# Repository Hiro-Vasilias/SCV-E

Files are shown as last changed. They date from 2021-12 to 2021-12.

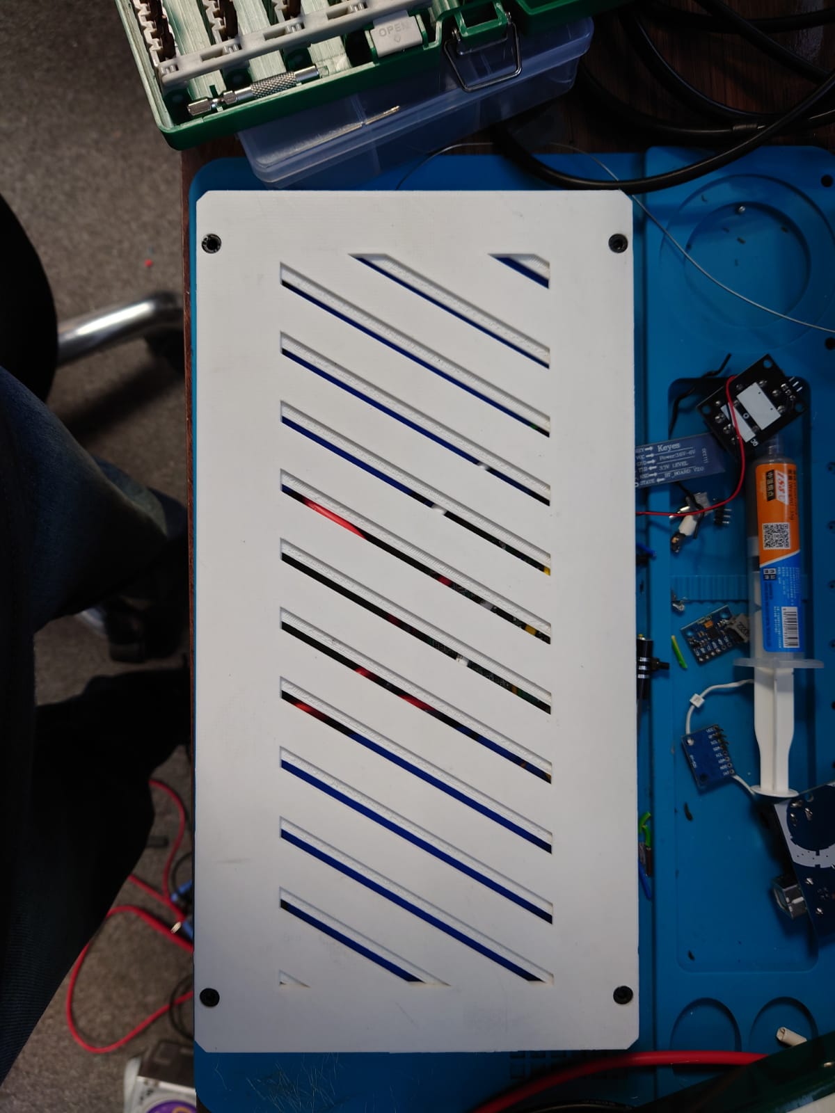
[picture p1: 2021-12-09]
Images/WhatsApp Image 2021-12-09 at 1.58.52 AM.jpeg

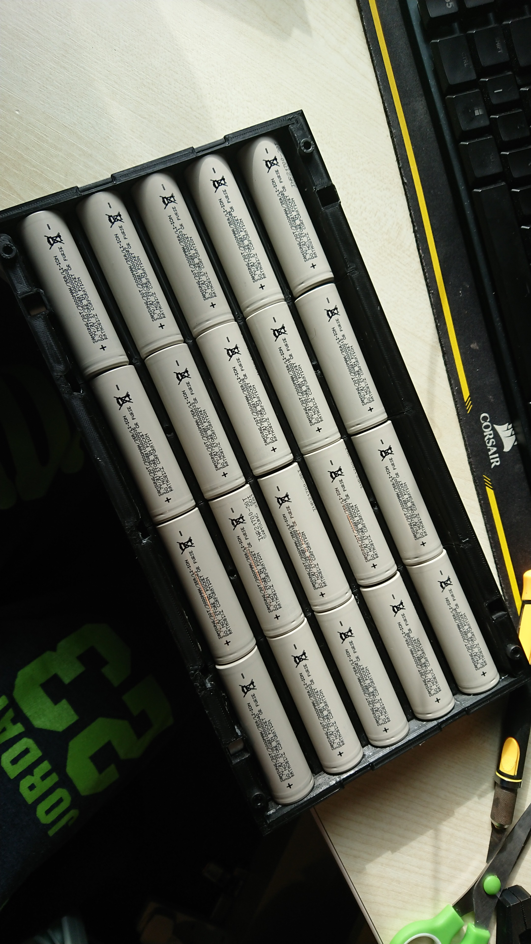
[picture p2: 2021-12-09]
Images/IMG-20210303-WA0010.jpg

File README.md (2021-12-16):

# SCV-E [Smart Construction Vehicle - Electric]
Modular vehicle for construction and transport

<<<<<<<<<<<<Contents>>>>>>>>>>>
  
  Documentation PROJ324.docx contains the documentation of the project submitted to the DLE.
  
  Proj324.xlsx contains the Budget costs and summary along with the Gantt chart.
  
  Buggy V2 V17.f3z contains the Design files Fusion 360
  
  Images Proj324 folder contains the images supporting this project.
  
  The rest shown are the programming code as shown in the document appendix

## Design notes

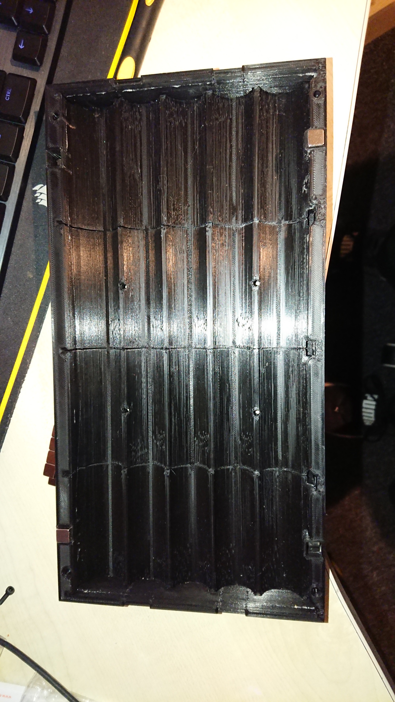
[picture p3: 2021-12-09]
Images/IMG-20210302-WA0009.jpg

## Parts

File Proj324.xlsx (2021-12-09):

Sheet: ProjectSchedule
Create a Project Schedule in this worksheet. Enter title of this project in cell B1. Information about how to use this worksheet, including instructions for screen readers and the author of this workbook is in the About worksheet. Continue navigating down column A to hear further instructions. | PROJ324 - SCV-E
Enter Company Name in cell B2. | Student 10588101
Enter the name of the Project Lead in cell B3. Enter the Project Start date in cell E3. Pooject Start: label is in cell C3. | Zil-E-Hasnain Shah | Project Start: |  | 2020-11-20
The Display Week in cell E4 represents the starting week to display in the project schedule in cell I4. The project start date is considered Week 1. To change the display week, simply enter a new week number in cell E4. The starting date for each week, starting with the display week from cell E4, starts in cell I4 and is auto calculated. There are 8 weeks represented in this view from cell I4 through cell BF4. You should not modify these cells. Display Week: label is in cell C4. |  | Display Week: |  | 1 |  | 2020-11-16 |  |  |  |  |  |  | 2020-11-23 |  |  |  |  |  |  | 2020-11-30 |  |  |  |  |  |  | 2020-12-07 |  |  |  |  |  |  | 2020-12-14 |  |  |  |  |  |  | 2020-12-21 |  |  |  |  |  |  | 2020-12-28 |  |  |  |  |  |  | 2021-01-04
Cells I5 through BL5 contain the day number for the week represented in the cell block above each date cell and are auto calculated. You should not modify these cells. Today's date is outlined in Red (hex #AD3815) from today's date in row 5 through the entire date column to the end of the project schedule. |  |  |  |  |  | 2020-11-16 | 2020-11-17 | 2020-11-18 | 2020-11-19 | 2020-11-20 | 2020-11-21 | 2020-11-22 | 2020-11-23 | 2020-11-24 | 2020-11-25 | 2020-11-26 | 2020-11-27 | 2020-11-28 | 2020-11-29 | 2020-11-30 | 2020-12-01 | 2020-12-02 | 2020-12-03 | 2020-12-04 | 2020-12-05 | 2020-12-06 | 2020-12-07 | 2020-12-08 | 2020-12-09 | 2020-12-10 | 2020-12-11 | 2020-12-12 | 2020-12-13 | 2020-12-14 | 2020-12-15 | 2020-12-16 | 2020-12-17 | 2020-12-18 | 2020-12-19 | 2020-12-20 | 2020-12-21 | 2020-12-22 | 2020-12-23 | 2020-12-24 | 2020-12-25 | 2020-12-26 | 2020-12-27 | 2020-12-28 | 2020-12-29 | 2020-12-30 | 2020-12-31 | 2021-01-01 | 2021-01-02 | 2021-01-03 | 2021-01-04 | 2021-01-05 | 2021-01-06
This row contains headers for the project schedule that follows below them. Navigate from B6 through BL 6 to hear the content. The first letter of each day of the week for the date above that heading, starts in cell I6 and continues through cell BL6. All project timeline charting is auto generated based on the start and end dates entered, using conditional formats. Do not modify content in cells within columns after column I starting with cell I7. | TASK | ASSIGNED TO | PROGRESS | START | END | M | T | W | T | F | S | S | M | T | W | T | F | S | S | M | T | W | T | F | S | S | M | T | W | T | F | S | S | M | T | W | T | F | S | S | M | T | W | T | F | S | S | M | T | W | T | F | S | S | M | T | W
Cell B8 contains the Phase 1 sample title. Enter a new Title in cell B8. Enter a name to assign the phase to, if it applies for your project, in cell C8. Enter Progress for the entire phase, if it applies for your project, in cell D8. Enter the start and end dates for the entire phase, if it applies for your project, in cells E8 and F8. The Gantt chart will automatically fill in the appropriate dates and shade according to the progress entered. To delete the phase and work only from tasks, simply delete this row. | Research Phase
Cell B9 contains the sample task "Task 1." Enter a new task name in cell B9. Enter a person to assign the task to in cell C9. Enter progres of the task in cell D9. A progress bar appears in the cell and is shaded according to the number in the cell. For example, 50 percent progress would shade half of the cell. Enter task start date in cell E9. Enter task end date in cell F9. A status bar shaded for the dates entered appears in blocks starting from cell I9 through BL9. | Construction vehicle |  | 100% | 2020-11-20 | 2020-11-20
Rows 10 through 13 repeat the pattern from row 9. Repeat the instructions from cell A9 for all task rows in this worksheet. Overwrite any sample data. A sample of another phase starts in cell A14. Continue entering tasks in cells A10 through A13 or go to cell A14 to learn more. | Batteries |  | 100% | 2020-12-01 | 2021-04-05
 | Crane |  | 100% | 2021-08-08 | 2021-11-20
 | Controller market |  | 100% | 2021-02-16 | 2021-03-21
 | Componets research |  | 100% | 2020-11-20 | 2021-01-01
 | Platform software |  | 100% | 2020-12-02 | 2020-12-04
The cell at right contains the Phase 2 sample title. You can create a new phase at any time within column B. This project schedule does not require phases. To remove the phase, simply delete the row. To create a new phase block in this row, enter a new Title in cell at right. To continue adding tasks to the phase above, enter a new row above this one and fill in the task data as in cell A9's instruction. Update the Phase details in cell at right based on cell A8's instruction. Continue navigating down column A cells to learn more. If you haven't added any new rows in this worksheet, you will find 2 additional sample phase blocks have been created for you in cells B20 and B26. Otherwise, navigate through column A cells to find the additional blocks. Repeat the instructions from cells A8 and A9 whenever you need to. | Design Phase
 | Initial CAD model of SCV |  | 100% | 2020-12-03 | 2021-01-12
 | Re-itereation of SCV |  | 100% | 2021-04-03 | 2021-07-25
 | PCB Circuit for SCV |  | 100% | 2021-10-01 | 2021-11-01
 | PCB Circuit for Controller |  | 100% | 2020-11-20 | 2021-02-16
 | CAD model of controller | 80% | 100% | 2021-02-20 | 2021-06-06
 | CAD model of base station |  | 100% | 2020-12-12 | 2021-03-25
Sample phase title block | Manufacturing Phase
 | 3D printing |  | 100% | 2020-12-05 | 2021-12-07
 | Assembling Controller |  | 100% | 2021-05-05 | 2021-08-08
 | Assembling base station | 80% | 100% | 2021-05-10 | 2021-05-15
 | Assembling SCV |  | 100% | 2021-05-16 | 2021-12-06
 | Programming Base station |  | 100% | 2021-09-01 | 2021-09-05
 | Programming SCV |  | 100% | 2021-07-06 | 2021-12-06
 | Assembling Makeshift Controller |  | 100% | 2021-11-26 | 2021-11-30
 | Programming Controller |  | 100% | 2021-12-01 | 2021-12-06
Sample phase title block | Testing
 | Controller |  | 100% | 2021-12-02 | 2021-12-06
 | SCV |  | 100% | 2021-12-02 | 2021-12-06
 | Deliverable
 | Main components delivered |  | 100% | 2021-01-01 | 2021-04-06
 | Second batch components delivered |  | 100% | 2021-05-15 | 2021-06-01
 | Third batch components delivered |  | 100% | 2021-10-02 | 2021-11-02
 | Disruption during project
 | Covid Self isolation #1 |  | 100% | 2020-12-26 | 2021-01-14
 | Covid Self isolation #2 |  | 100% | 2021-08-14 | 2021-08-30
 | Family Death Covid |  | 100% | 2021-05-06 | 2021-05-06
 | Family Death Covid |  | 100% | 2021-08-07 | 2021-08-07
This is an empty row
This row marks the end of the Project Schedule. DO NOT enter anything in this row. Insert new rows ABOVE this one to continue building out your Project Schedule. | Insert new rows ABOVE this one

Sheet: BUDGET SUMMARY
 |  | Itemized Expenses
PROJ324 | PROJECT BUDGET
PROJECT INFORMATION
Project Name | SCV-E
Project Description | Dump Truck Type Buggy with Crane lifter and Live Video Feedback, Charging base and Custom Controller included
Contractor | -
Student ID | 10588101
Student Name | Hasnain Shah
OneNote Link | PROJECT SHOWCASE (https://liveplymouthac.sharepoint.com/sites/Projects-PROJ324PROJ325/_layouts/15/Doc.aspx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)
SuperVisor | Shakil Awan Ahmed
FullFilled Date | 9th december 2021
FINANCIAL STATUS
Planned Amount | £500.00
Sponsored Amount | £250.00
Additional Amount put in | £1500.00
Loaned Amount | £500.00
Total Allotted Funds | £2750.00
Funds Used To Date | £2740.91
Project Cost | £667.85
Funds Remaining | £9.09

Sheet: ITEMIZED EXPENSES
 |  |  |  |  |  |  |  |  | Budget Summary
LIST | OF EXPENSES
PROJECT FUNDS ALLOTTED |  | FUNDS USED TO DATE |  |  | PROJECT COST |  |  | FUNDS REMAINING
£2750.00 |  | £2740.91 |  |  | £667.85 |  |  | £9.09
Item | Supplier | Category | Type | QTY | Purchase Cost | Price Per QTY | Used QTY | Used Cost
TS5828s 200MW 5.8G 40ch FPV Camera | AliExpress | Materials | Buggy | 1 | £17.78 | £17.78 | 1 | £17.78
50 Pairs Metal Battery Spring plate | AliExpress | Materials | Buggy | 50 | £3.33 | £0.07 | 0 | £0.00
GT-24 Wireless module 2.4G NRF24L01 | AliExpress | Materials | Buggy | 1 | £2.24 | £2.24 |  | £0.00
Mechanic UV Solder Mask INK PCB | AliExpress | Equipment | All | 1 | £3.63 | £3.63 | 0.5 | £1.81
N35 Neodymium magnets | AliExpress | Materials | Base Station | 50 | £4.25 | £0.09 | 4 | £0.34
N50 Neodymium magnets | AliExpress | Materials | Buggy | 20 | 8 | £0.40 | 8 | £3.20
50N Solenoid Electromagnet 5V + IP65 | AliExpress | Materials | Buggy | 1 | £2.68 | £2.68 | 1 | £2.68
25N Solenoid Electromagnet 5V + IP65 | AliExpress | Materials | None | 1 | £1.97 | £1.97 | 0 | £0.00
Crocodile Clips | AliExpress | Equipment | All | 10 | £1.27 | £0.13 | 0 | £0.00
Mechanic Paste Flux 10CC SMD PCB | AliExpress | Equipment | All | 2 | £3.75 | £1.88 | 0.5 | £0.94
Alligator test clip to Jumper cable 30cm | AliExpress | Equipment | All | 5 | £2.16 | £0.43 | 5 | £2.16
Toggle Switch 125V 6A ON-ON 2POS+3PIN | AliExpress | Materials | Controller | 5 | £2.55 | £0.51 |  | £0.00
Potentiometer 10K ohm | AliExpress | Materials | Controller | 5 | £1.91 | £0.38 |  | £0.00
100x100 mm Thermal Pad heatsink | AliExpress | Materials | Buggy | 2 | £6.71 | £3.35 | 2 | £6.71
4S 40A BMS LIPO with balancer | AliExpress | Materials | Buggy | 1 | £3.33 | £3.33 | 1 | £3.33
SMD LED 5730 kit | AliExpress | Materials | None | 100 | £2.10 | £0.02 |  | £0.00
BGA Reballing 1 Bottle 0.76 mm | AliExpress | Materials | None | 1 | £1.37 | £1.37 | 0 | £0.00
GT-24 Wireless module 2.4G NRF24L01 | AliExpress | Materials | Controller | 1 | £2.24 | £2.24 | 1 | £2.24
Type C PD3.0 Trigger Spoof | AliExpress | Materials | None | 1 | £5.74 | £5.74 | 1 | £5.74
15W Qi Wireless charger | AliExpress | Materials | Base Station | 1 | £8.28 | £8.28 | 1 | £8.28
Battery Insulator gasket 1000x120 mm | AliExpress | Materials | B+C | 1 | £1.65 | £1.65 |  | £0.00
4PCS 110x48 mm 1/10 Wheel set | AliExpress | Materials | Buggy | 4 | £14.90 | £3.73 | 4 | £14.90
Push button Vertical Set 4 pin | AliExpress | Materials | Controller | 100 | £2.56 | £0.03 | 10 | £0.26
4x360 Servo 35KG | AliExpress | Materials | Buggy | 4 | £30.59 | £7.65 | 5 | £38.24
ESD Heat soldering Mat | AliExpress | Materials | All | 1 | £8.29 | £8.29 |  | £0.00
DC Motor 5-200 rpm Hall Encoder | AliExpress | Materials | Buggy | 4 | £23.21 | £5.80 | 4 | £23.21
Micro Switches assorted 10 type ea | AliExpress | Materials | Controller | 100 | £3.55 | £0.04 |  | £0.00
JST-XH JST + Dupont connector Kit + crimping tool | AliExpress | Materials | All | 1080 | £15.94 | £0.01 | 5 | £0.07
5000 mAh Li-po Batteries 3.7V | AliExpress | Materials | Controller | 4 | £11.73 | £2.93 | 0 | £0.00
10000 mAh Li-po Batteries 3.7V | AliExpress | Materials | None | 2 | £9.60 | £4.80 | 0 | £0.00
Panasonic 21700 4800mAh +PCB 40A | AliExpress | Loss (Scammed) | Buggy | 40 | £80.31 | £2.01 | 0 | £0.00
Carbon Fiber Hydro dip | AliExpress | Materials | Controller | 1 | £5.92 | £5.92 |  | £0.00
Joystick 3D analog PS2 | AliExpress | Materials | Controller | 4 | £2.84 | £0.71 | 2 | £1.42
SMD LED 5050 RGB | AliExpress | Materials | None | 100 | £1.66 | £0.02 |  | £0.00
Type C PD3.0 20V | AliExpress | Materials | Base Station | 1 | £1.45 | £1.45 | 1 | £1.45
Type C PD3.0 9V | AliExpress | Materials | Controller | 1 | £1.45 | £1.45 | 1 | £1.45
GY-521 MPU 6050 accelerometer | AliExpress | Materials | Controller | 1 | £6.75 | £6.75 | 1 | £6.75
E-DA TPU 1KG 1.75 mm Filament (Price per gram) | Amazon | Materials | All | 1000 | £20.98 | £0.02 |  | £0.00
Gorilla Wood Glue 1L | Amazon | Equipment | Base Station | 1 | £9.00 | £9.00 |  | £0.00
Gorilla Super Glue 12g | Amazon | Equipment | All | 1 | £4.80 | £4.80 |  | £0.00
Gorilla Glue Contact Adhesive 75g | Amazon | Equipment | B+BS | 1 | £6.68 | £6.68 |  | £0.00
Dremel Moto scroll saw MS20 | Amazon | Equipment | All | 1 | £100.26 | £100.26 |  | £0.00
Banana Plug connector | Amazon | Materials | Buggy | 20 | £7.99 | £0.40 | 10 | £4.00
Anycubic 3D printer PLA 1KG | Amazon | Materials | All | 1000 | £21.99 | £0.02 |  | £0.00
LACO125AMZ-LA-CO Flux paste 125g | Amazon | Materials | All | 1 | £5.75 | £5.75 |  | £0.00
Hurricane 3 pc Pliers Set | Amazon | Equipment | All | 3 | £18.99 | £6.33 |  | £0.00
Copper Sheet 0.4x300x210 mm | Amazon | Materials | Buggy | 2 | £22.00 | £11.00 | 1.5 | £16.50
DC PSU LAB power bench 30V-10A max | Amazon | Equipment | All | 1 | £72.99 | £72.99 |  | £0.00
Resistor kit 1% 1/4 | Amazon | Materials | All | 1050 | £12.99 | £0.01 | 20 | £0.25
LED 5 mm | Amazon | Materials | B+C | 500 | £6.99 | £0.01 |  | £0.00
PLA Filament 1 KG Generic Gray | Volt3D | Materials | All | 1000 | £10.00 | £0.01 | 1 | £0.01
PLA Filament 1 KG Evryone Black | Amazon | Materials | All | 1000 | £17.99 | £0.02 | 1 | £0.02
PLA Filament 1KG Evryone Glitter Black | Amazon | Materials | All | 1000 | £17.99 | £0.02 |  | £0.00
Wifi Router Attenna IPEX4 | Amazon | Materials | Controller | 2 | £8.49 | £4.25 | 2 | £8.49
Arduino Nano 33 BLE Sense [ABX00031] | Amazon | Materials | Controller | 1 | £35.40 | £35.40 | 0 | £0.00
5.8G mini 72CH 200mW Eachine VTX03 | Banggood | Materials | Buggy | 1 | £8.96 | £8.96 |  | £0.00
Foxeer Razer 5MP HD Camera | Banggood | Materials | Buggy | 1 | £16.78 | £16.78 | 1 | £16.78
RX5805 5.8Ghz 48ch 480x320 5'' monitor | Banggood | Materials | Controller | 1 | £20.45 | £20.45 | 0 | £0.00
Simax3D Magnetic 3D printer Bed | Banggood | Replacement | All | 1 | £7.70 | £7.70 |  | £0.00
Hotend 24V 40W (creality) | Banggood | Replacement | All | 1 | £8.30 | £8.30 |  | £0.00
21700 Insulators | Fogstar Wholesale UK | Materials | Buggy | 100 | £4.00 | £0.04 | 1 | £0.04
21700 PVC Wraps - Black | Fogstar Wholesale UK | Materials | Buggy | 40 | £2.10 | £0.05 | 1 | £0.05
Samsung 21700 30T - 3.7V 30A | Fogstar Wholesale UK | Materials | Buggy | 40 | £115.60 | £2.89 | 22 | £63.58
Efest V8 - 21700 cell charger | Fogstar Wholesale UK | Equipment | All | 1 | £24.45 | £24.45 |  | £0.00
MDF 2440x1220 | B&Q UK | Materials | Base Station | 3 | £45.00 | £15.00 | 2.7 | £40.50
Controller Custom PCB [Y1-3442490B] | JCLB | Materials | Controller | 5 | £15.36 | £3.07 | 2 | £6.14
Micro JST PH2.0 2-pin plugs 10cm | Amazon | Materials | Controller | 20 | £5.99 | £0.30 |  | £0.00
Choetecth USB C PD100W | Amazon | Equipment | Base Station | 1 | £49.99 | £49.99 | 1 | £49.99
Inductor 0.5W 1/2W | Amazon | Materials | All | 200 | £12.99 | £0.06 | 2 | £0.13
3 pin SPDT mini slide switch | Amazon | Materials | All | 55 | £7.49 | £0.14 | 2 | £0.27
Capacitor assortment kit | Amazon | Materials | All | 600 | £15.99 | £0.03 | 2 | £0.05
22AWG PVC 9M spool Blue (Price per cm) | Amazon | Materials | All | 900 | £2.33 | £0.002592222222 | 30 | £0.08
22AWG PVC 9M spool Black (Price per cm) | Amazon | Materials | All | 900 | £2.33 | £0.002588888889 | 40 | £0.10
22AWG PVC 9M spool Green (Price per cm) | Amazon | Materials | All | 900 | £2.33 | £0.002588888889 | 50 | £0.13
22AWG PVC 9M spool White (Price per cm) | Amazon | Materials | All | 900 | £2.33 | £0.002588888889 | 10 | £0.03
22AWG PVC 9M spool Yellow(Price per cm) | Amazon | Materials | All | 900 | £2.33 | £0.002588888889 | 5 | £0.01
22AWG PVC 9M spool Red (Price per cm) | Amazon | Materials | All | 900 | £2.33 | £0.002588888889 | 40 | £0.10
Arduino Mega 2560 Rev3 [A000067] | Amazon | Materials | Buggy | 1 | £35.70 | £35.70 | 0 | £0.00
YIXISI High Temperature Kapton Tape 3mm | Amazon | Materials | All | 330 | £1.76 | £0.01 |  | £0.00
YIXISI High Temperature Kapton Tape 6mm | Amazon | Materials | All | 330 | £1.76 | £0.01 |  | £0.00
YIXISI High Temperature Kapton Tape 8mm | Amazon | Materials | All | 330 | £1.76 | £0.01 |  | £0.00
YIXISI High Temperature Kapton Tape 10mm | Amazon | Materials | All | 330 | £1.76 | £0.01 |  | £0.00
YIXISI High Temperature Kapton Tape 12mm | Amazon | Materials | All | 330 | £1.76 | £0.01 |  | £0.00
YIXISI High Temperature Kapton Tape 20mm | Amazon | Materials | All | 330 | £1.76 | £0.01 | 30 | £0.16
Arduino Mega R3 Elegoo | Amazon | Materials | Buggy | 1 | £11.89 | £11.89 | 1 | £11.89
PLA Filament ppx Black | Amazon | Materials | Controller | 1 | 18.38 | £18.38 | 1 | £18.38
First Aid Kit pack of 100 | Amazon | Safety | Human | 100 | 9.49 | £0.09 | 12 | £1.14
The One Paint Satin White + Dark Grey# | Amazon | Materials | Base Station | 1 | 37.98 | £37.98 | 0 | £0.00
Electric paint sprayer | Amazon | Equipment | All | 1 | 32.53 | £32.53 |  | £0.00
MDF Primer White | Amazon | Materials | Base Station | 1 | 9.9 | £9.90 |  | £0.00
Chisel Set tools | Amazon | Equipment | All | 1 | 27.99 | £27.99 | 0.2 | £5.60
Belt Sander Rent | Machinemarkt | Equipment | Base Station | 1 | 15.99 | £15.99 | 0 | £0.00
Geetech PETG Filament | Amazon | Materials | All | 1 | 23.99 | £23.99 | 1 | £23.99
Elegoo Mars Pro SLA printer | Amazon | Equipment | All | 1 | 130 | £130.00 |  | £0.00
Elegoo LCD UV 405nm ABS | Amazon | Materials | All | 1 | 38 | £38.00 |  | £0.00
Rubber Mallet fiberglas | Amazon | Equipment | All | 1 | 14.95 | £14.95 |  | £0.00
Primacreator Value UV FLEX resin | Amazon | Materials | All | 1 | 34.38 | £34.38 |  | £0.00
10 pin rainbow flat ribbon cable | Amazon | Materials | All | 1 | 7.19 | £7.19 |  | £0.00
Tronxy X5SA pro printer | Machinemarkt | Equipment | All | 1 | 339.98 | £339.98 | 0.1 | £34.00
Tecbears PLA Filament | Amazon | Materials | All | 5 | 64.95 | £12.99 | 4 | £51.96
Tecbears Petg Filament | Amazon | Materials | All | 1 | 11.99 | £11.99 |  | £0.00
Ball Bearing 8mm x22 mm x7 mm | Amazon | Materials | All | 8 | 6.49 | £0.81 | 3 | £2.43
HSS step drill bits | Amazon | Equipment | All | 3 | 12.34 | £4.11 |  | £0.00
GT2 Pulley 8mm bore 6mm width | Amazon | Materials | All | 10 | 7.99 | £0.80 | 4 | £3.20
Deburing tool | Amazon | Equipment | All | 1 | 12.73 | £12.73 |  | £0.00
3D printer Glass platform holder | Amazon | Equipment | All | 100 | 7.99 | £0.08 | 4 | £0.32
Cable ties 100 | Amazon | Materials | All | 100 | 2.99 | £0.03 | 25 | £0.75
Tool star lock washers stainless steel | Amazon | Materials | All | 300 | 10.44 | £0.03 | 3 | £0.10
Dremel Workstation 220 | Amazon | Equipment | All | 1 | 29.24 | £29.24 |  | £0.00
PCA9685 16 channel | Amazon | Materials | Buggy | 2 | 7.59 | £3.79 | 1 | £3.79
360 pcs dupont wire | Amazon | Materials | All | 360 | 9.99 | £0.03 | 100 | £2.77
L298N stepper motor driver | Amazon | Materials | Buggy | 5 | 9.99 | £2.00 | 3 | £5.99
Fuse wire | Amazon | Materials | Buggy | 3 | 2.9 | £0.97 | 1 | £0.97
Fuse holder | Amazon | Materials | Buggy | 1 | 2.99 | £2.99 | 1 | £2.99
Reed Magnetic switch | Amazon | Materials | Buggy | 10 | 7.99 | £0.80 |  | £0.00
150 mm linear actuator | Amazon | Materials | Buggy | 1 | 29.9 | £29.90 | 1 | £29.90
Dremel MS53 Saw blades | Amazon | Equipment | All | 5 | 6 | £1.20 | 3 | £3.60
Arduino BLE-NANO replica | Amazon | Materials | Controller | 1 | 22.6 | £22.60 | 1 | £22.60
Helping hands third hand soldering tool | Amazon | Equipment | All | 1 | 32.99 | £32.99 |  | £0.00
AZDelivery NRF24L01 | Amazon | Materials | All | 10 | 10.49 | £1.05 | 2 | £2.10
Metal Servo Arm 25T | Amazon | Materials | Buggy | 6 | 7.59 | £1.26 | 4 | £5.06
Hotend Nozzle | Amazon | Equipment | All | 10 | £6.99 | £0.70 | 3 | £2.10
Kywoo Tycoon Max 3D printer | Machinemarkt | Equipment | All | 1 | 447.99 | £447.99 | 0.05 | £22.40
FPV monitor 5.8GHZ LCD | Amazon | Materials | Controller | 1 | 42.87 | £42.87 | 1 | £42.87
Carbon steel Ball Bearing | Amazon | Materials | All | 40 | £10.88 | £0.27 | 4 | £1.09
Rubbing Alcohol IPA | Amazon | Equipment | All | 2 | £30.99 | £15.49 | 1 | £15.49
Total |  |  |  |  | £2740.91 | £1983.63 |  | £667.85
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

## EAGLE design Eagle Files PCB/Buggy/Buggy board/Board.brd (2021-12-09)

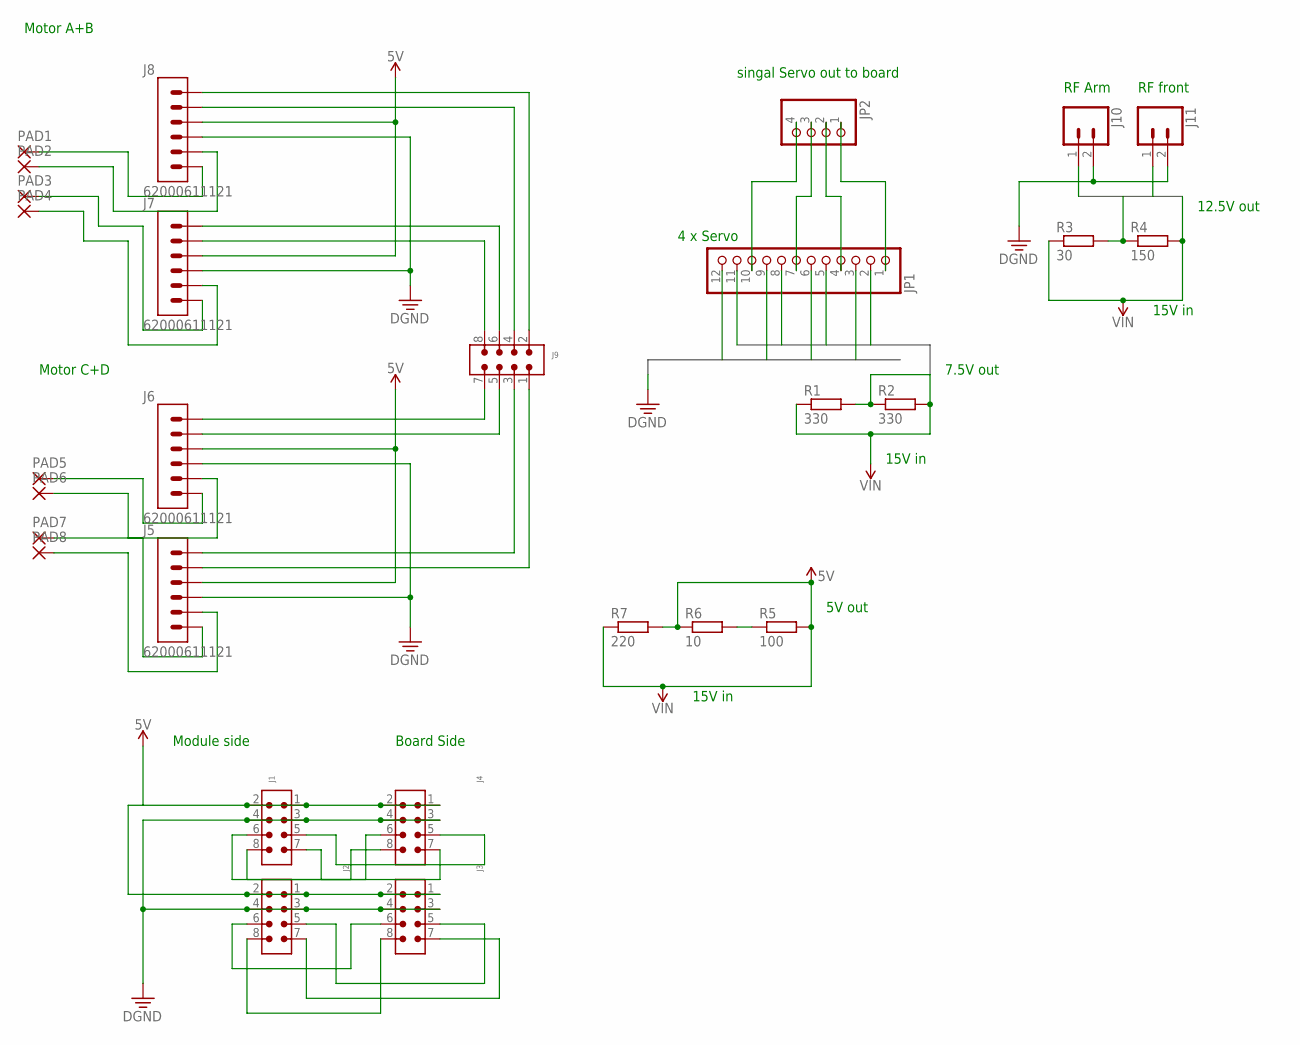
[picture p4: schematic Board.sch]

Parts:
J1, J2, J3, J4, J9: 6130XX21021_61300821021; 61300821021
J5, J6, J7, J8: 62000611121
J10, J11: CONN_02LOCK_LONGPADS; 1X02_LOCK_LONGPADS
JP1: PINHD-1X12; 1X12
JP2: PINHD-1X4/90; 1X04/90
PAD1, PAD2, PAD3, PAD4, PAD5, PAD6, PAD7, PAD8: 3,17/1,3
R1, R2: 330; 0207/10
R3: 30; 0207/10
R4: 150; 0207/10
R5: 100; 0207/10
R6: 10; 0207/10
R7: 220; 0207/10

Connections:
5V: J1.1, J1.2, J2.1, J2.2, J3.1, J3.2, J4.1, J4.2, J5.3, J6.3, J7.3, J8.3
B$1: JP1.3, JP1.6, JP1.9, JP1.12
B$2: JP1.2, JP1.5, JP1.8, JP1.11, R1.1, R1.2, R2.1, R2.2
B$3: J10.1, J11.1, R3.1, R3.2, R4.1, R4.2
DGND: J1.3, J1.4, J2.3, J2.4, J3.3, J3.4, J4.3, J4.4, J5.4, J6.4, J7.4, J8.4, J10.2, J11.2
unnamed: J1.8, J4.8
unnamed: J1.6, J4.6
unnamed: J1.7, J4.7
unnamed: J2.5, J3.5
unnamed: J1.5, J4.5
unnamed: J2.7, J3.7
unnamed: J2.8, J3.8
unnamed: J2.6, J3.6
unnamed: J6.6, PAD5.1
unnamed: J5.6, PAD7.1
unnamed: J6.5, PAD6.1
unnamed: J5.5, PAD8.1
unnamed: J8.6, PAD1.1
unnamed: J8.5, PAD2.1
unnamed: J7.6, PAD3.1
unnamed: J7.5, PAD4.1
unnamed: J5.2, J9.1
unnamed: J5.1, J9.3
unnamed: J6.2, J9.5
unnamed: J6.1, J9.7
unnamed: J7.2, J9.8
unnamed: J7.1, J9.6
unnamed: J8.2, J9.4
unnamed: J8.1, J9.2
unnamed: JP1.1, JP2.1
unnamed: JP1.4, JP2.2
unnamed: JP1.7, JP2.3
unnamed: JP1.10, JP2.4
unnamed: R5.1, R6.2
VIN: R5.2, R6.1, R7.1, R7.2

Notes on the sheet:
Module side
Board Side
Motor A+B
Motor C+D
15V in
7.5V out
4 x Servo
singal Servo out to board
RF front
RF Arm
12.5V out
5V out

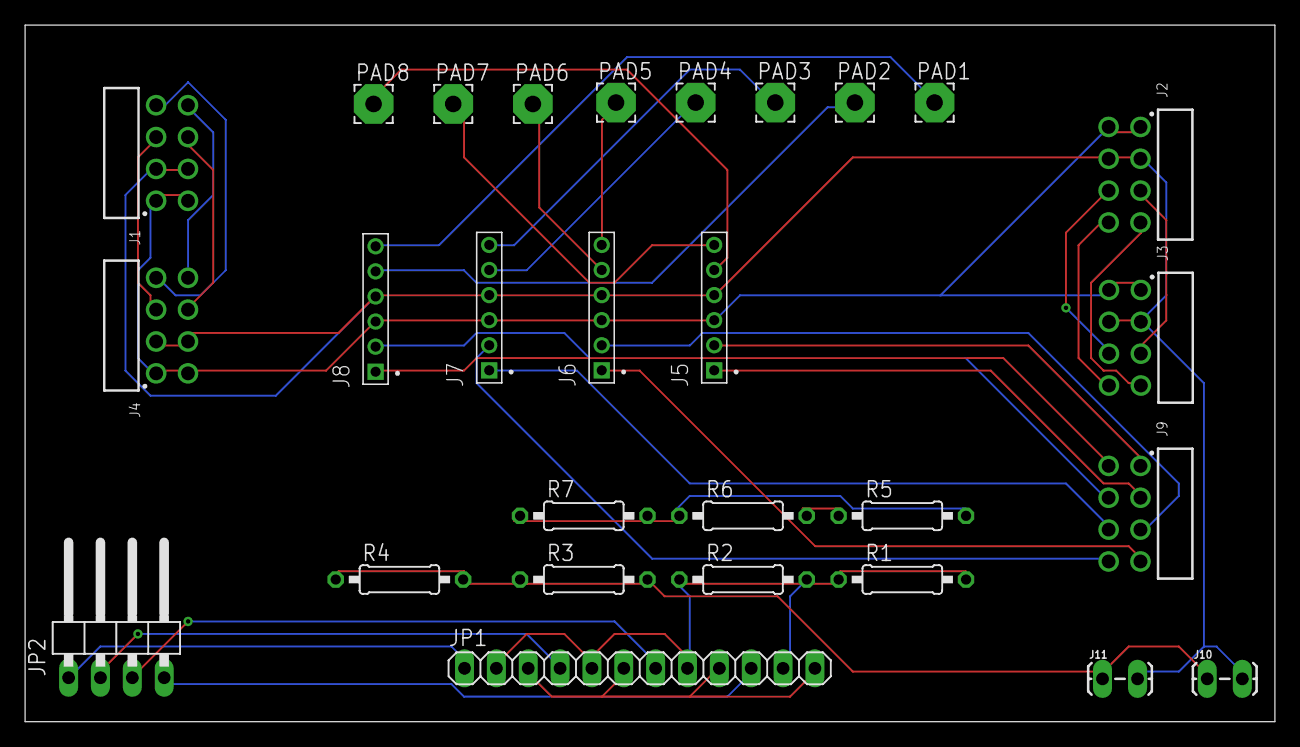
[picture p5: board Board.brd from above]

Board: 2 copper layers, 99.7 x 55.5 mm, 28 parts (0 on the bottom side), 35 nets.

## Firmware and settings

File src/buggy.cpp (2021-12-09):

#include <SPI.h>
#include <nRF24L01.h>
#include <RF24.h>
#include <Adafruit_PWMServoDriver.h>
#include <Wire.h>
#include <Servo.h>

const byte address[6] = "00001"; // address of the radio to receive the data on
RF24 radio(10, 11);
bool radioReady = false;
int mode = 1;                    // The default controller mode is set to 1. This can be changed by pressing other buttons on the remote.

String directionX = "CENTRE";    // Default analog stick position on the X axis
int directionXSpeed = 0;         // The speed of that direction. e.g a bit to the left will be speed 1. More to the left will increase the speed. Max speed is 4.
String directionY = "CENTRE";    // Default analog stick position on the Y axis
int directionYSpeed = 0;         // The speed of that direction. e.g a bit downwards will be speed 1. Fully downwards stick will increase the speed. Max speed is 4.

Servo craneservo;
Servo magnetropeservo;

bool magnet_state = false; //(FALSE IS OFF)

// Components output pins on the arduino Board
#define MAGNET_INPUT 26

#define LINIER_ACTUATOR_A 36
#define LINIER_ACTUATOR_PIN_1 30
#define LINIER_ACTUATOR_PIN_2 28

//#define MOTOR_RIGHT_TOP_A 13
#define MOTOR_RIGHT_TOP_1 37
#define MOTOR_RIGHT_TOP_2 35

#define MOTOR_RIGHT_BOTTOM_1 49
#define MOTOR_RIGHT_BOTTOM_2 45

#define MOTOR_LEFT_TOP_1 43
#define MOTOR_LEFT_TOP_2 47

#define MOTOR_LEFT_BOTTOM_1 39
#define MOTOR_LEFT_BOTTOM_2 41

int pos = 0;        // variable to store the crane servo position
int ropepos = 0;    // variable to store the magnet rope servo position

void setup() {
  // Initialise Serial first
  Serial.begin(9600);  // Baud rate

  /**
     The functions below allows to setup the components with their respective pins. It sets also the pins to their default state
  */
  setupRadio();
  setupMotors();
  setupActuator();
  setupServo();
  setupMagnet();

}

void setupServo() {

  // Setting up pins for the servos
  craneservo.attach(22);
  magnetropeservo.attach(24);
}

void setupRadio() {
  // Pin modes
  // Configure the Radio
  int failCount = 0;
  while (!radioReady && failCount < 10) {
    radioReady = radio.begin();
    if (!radioReady) {
      failCount++;
      Serial.print("Radio Initialisation Failed ");
      Serial.print(failCount);
      Serial.println(" times.");
    } else {
      Serial.println(" radio ready.");
    }
  }
  radio.openReadingPipe(0, address);   //Setting the address at which we will receive the data
  radio.setPALevel(RF24_PA_MIN);       //You can set this as minimum or maximum depending on the distance between the transmitter and receiver.
  radio.startListening();              //Setting the radio in the receiving mode
}


void setupMotors()
{

  /**
     setup motors on their respective pins and set the initial values to off
  */

  pinMode(MOTOR_RIGHT_TOP_1, OUTPUT);
  pinMode(MOTOR_RIGHT_TOP_2, OUTPUT);
  digitalWrite(MOTOR_RIGHT_TOP_1, LOW);
  digitalWrite(MOTOR_RIGHT_TOP_2, LOW);


  pinMode(MOTOR_RIGHT_BOTTOM_1, OUTPUT);
  pinMode(MOTOR_RIGHT_BOTTOM_2, OUTPUT);
  digitalWrite(MOTOR_RIGHT_BOTTOM_1, LOW);
  digitalWrite(MOTOR_RIGHT_BOTTOM_2, LOW);

  pinMode(MOTOR_LEFT_TOP_1, OUTPUT);
  pinMode(MOTOR_LEFT_TOP_2, OUTPUT);
  digitalWrite(MOTOR_LEFT_TOP_1, LOW);
  digitalWrite(MOTOR_LEFT_TOP_2, LOW);

  pinMode(MOTOR_LEFT_BOTTOM_1, OUTPUT);
  pinMode(MOTOR_LEFT_BOTTOM_2, OUTPUT);
  digitalWrite(MOTOR_LEFT_BOTTOM_1, LOW);
  digitalWrite(MOTOR_LEFT_BOTTOM_2, LOW);

}

void setupActuator()
{
  /**
    setup the actuator on the correct pins
  */

  pinMode(LINIER_ACTUATOR_A, OUTPUT);
  pinMode(LINIER_ACTUATOR_PIN_1, OUTPUT);
  pinMode(LINIER_ACTUATOR_PIN_2, OUTPUT);
  digitalWrite(LINIER_ACTUATOR_PIN_1, LOW);
  digitalWrite(LINIER_ACTUATOR_PIN_2, LOW);
}

void setupMagnet()
{
  pinMode(MAGNET_INPUT, OUTPUT);
}

void loop()
{
  readCommandsFromRadio();
  delay(5);

  // For debugging persos to understand what is being received from the controller
  printControllerValues();


  // Allow only one mode at a time because of a single analog stick. mode will be set depending on what is received from the controller

  if (mode == 1) {
    controlBuggy();
  } else if (mode == 2) {
    controlCraneArm();
  } else if (mode == 3) {
    controlCraneHeight();
  } else if (mode == 4) {
    controlCraneRope();
  } else if (mode == 5) {
    toggleMagnet();
  }

}

void toggleMagnet() {

   // If magenet_state = false (off) turn it on. Else turn it off
    if (magnet_state = false) {
      magnet_state = true;
      digitalWrite(MAGNET_INPUT, HIGH);
    } else {
      magent_state = false;
      digitalWrite(MAGNET_INPUT, LOW);
    }
}
void controlCraneArm() {

  if (directionY == "UP") {

    // Telling the servo to go up a bit
    for (int x = 0; x < 10; x++) {
      pos = pos + 1;
      craneservo.write(pos);
      Serial.println("Crane Servo Up");
      Serial.println(pos);
      delay(20);
    }
  } else if (directionY == "DOWN") {

     // Telling the crane servo to go down

    for (int y = 10; y > 0; y--) {
      pos = pos - 1;
      craneservo.write(pos);
      Serial.println("Crane Servo Down");
      Serial.println(pos);
      delay(20);
    }
  }
}

void controlCraneRope() {

      // Telling the servo to go up a bit

  if (directionY == "UP") {
    for (int x = 0; x < 10; x++) {
      ropepos = ropepos + 1;
      magnetropeservo.write(ropepos);
      Serial.println("UP");
      Serial.println(ropepos);
      delay(20);
    }
  } else if (directionY == "DOWN") {

      // Telling the crane servo to go down

    for (int y = 10; y > 0; y--) {
      ropepos = ropepos - 1;
      magnetropeservo.write(ropepos);
      delay(20);
      Serial.println("Down");
      Serial.println(ropepos);
    }
  }
}

void controlCraneHeight() {

  if (directionY == "UP") {
    pinMode(LINIER_ACTUATOR_A, HIGH);

    digitalWrite(LINIER_ACTUATOR_PIN_1, HIGH);
    digitalWrite(LINIER_ACTUATOR_PIN_2, LOW);

    delay(20);
  } else if (directionY == "DOWN") {
    pinMode(LINIER_ACTUATOR_A, HIGH);

    digitalWrite(LINIER_ACTUATOR_PIN_1, LOW);
    digitalWrite(LINIER_ACTUATOR_PIN_2, HIGH);

    delay(20);
  } else {
    pinMode(LINIER_ACTUATOR_A, LOW);

    digitalWrite(LINIER_ACTUATOR_PIN_1, LOW);
    digitalWrite(LINIER_ACTUATOR_PIN_2, LOW);
  }

}


void controlBuggy() {

  /**
   * The movement of the buggy works like as a tank. e.g to go right we go forwards with the left motors and backwards with the right ones.
   */
  if (directionX == "LEFT") {
    forwardRightMotors();
    backwardsLeftMotors();
    delay(20);
  } else if (directionX == "RIGHT") {

    backwardsRightMotors();
    forwardLeftMotors();

    delay(20);
  } else if (directionY == "UP") {
    forwardRightMotors();
    forwardLeftMotors();
    delay(20);
  } else if (directionY == "DOWN") {
    backwardsRightMotors();
    backwardsLeftMotors();

    delay(20);
  } else {

    /**
     * if no direction is give we put it to a stop
     */
    digitalWrite(MOTOR_RIGHT_TOP_1, LOW);
    digitalWrite(MOTOR_RIGHT_TOP_2, LOW);
    digitalWrite(MOTOR_RIGHT_BOTTOM_1, LOW);
    digitalWrite(MOTOR_RIGHT_BOTTOM_2, LOW);
    digitalWrite(MOTOR_LEFT_TOP_1, LOW);
    digitalWrite(MOTOR_LEFT_TOP_2, LOW);
    digitalWrite(MOTOR_LEFT_BOTTOM_1, LOW);
    digitalWrite(MOTOR_LEFT_BOTTOM_2, LOW);
  }

}

void forwardRightMotors() {

  digitalWrite(MOTOR_RIGHT_TOP_1, LOW);
  digitalWrite(MOTOR_RIGHT_TOP_2, HIGH);
  digitalWrite(MOTOR_RIGHT_BOTTOM_1, LOW);
  digitalWrite(MOTOR_RIGHT_BOTTOM_2, HIGH);

}

void forwardLeftMotors() {

  digitalWrite(MOTOR_LEFT_TOP_1, LOW);
  digitalWrite(MOTOR_LEFT_TOP_2, HIGH);
  digitalWrite(MOTOR_LEFT_BOTTOM_1, LOW);
  digitalWrite(MOTOR_LEFT_BOTTOM_2, HIGH);

}


void backwardsRightMotors() {

  digitalWrite(MOTOR_RIGHT_TOP_1, HIGH);
  digitalWrite(MOTOR_RIGHT_TOP_2, LOW);
  digitalWrite(MOTOR_RIGHT_BOTTOM_1, HIGH);
  digitalWrite(MOTOR_RIGHT_BOTTOM_2, LOW);

}

void backwardsLeftMotors() {

  digitalWrite(MOTOR_LEFT_TOP_1, HIGH);
  digitalWrite(MOTOR_LEFT_TOP_2, LOW);
  digitalWrite(MOTOR_LEFT_BOTTOM_1, HIGH);
  digitalWrite(MOTOR_LEFT_BOTTOM_2, LOW);

}

void readCommandsFromRadio() {
  if (radio.available())              //Looking for the data.
  {
    char text[32] = "";                 //Saving the incoming data
    radio.read(&text, sizeof(text));
    String stringCommand = String(text);

    /**
     * Only set the mode if the command start with an M. 
     * The controller send the command in the following format M=1X=1Y=1
     * 
     * M can be from 1 to 5 which stand for MODE
     * X = the potensiometer value from the analog stick. Values can be 1-9 (4 = CENTER)
     * Y = the potensiometer value from the analog stick. Values can be 1-9 (4 = CENTER)
     */
    if (stringCommand.charAt(0) == 'M') {  

      // MODE
      setMode(stringCommand.charAt(2) - '0'); // Read the THIRD charactar of the command.  "- '0'" is to convert the charactar into an integer
      setDirectionAndSpeedX((stringCommand.charAt(5) - '0')); // Read the 6TH charactar of the command.  "- '0'" is to convert the charactar into an integer
      setDirectionAndSpeedY(stringCommand.charAt(8) - '0'); //Read the 9TH
    }
  }
}

void setMode(int mode) {
  mode = mode;
}

void setDirectionAndSpeedX(int x) {

  /**
   *  The analog sticks potentio meters send a value from 1-9 and. 4 is the centre value. 
   *  Set the speed and the direction based on the value
   */
  
  if (x > 4) {
    directionX = "LEFT";
    directionXSpeed = map(x, 4, 9, 0, 4);
  } else if (x < 4)  {
    directionX = "RIGHT";
    directionXSpeed = map(x, 4, 0, 0, 4);
  } else {
    directionX = "CENTRE";
    directionXSpeed = 0;
  }

  delay(20);
}

void setDirectionAndSpeedY(int y) {

    /**
   *  The analog sticks potentio meters send a value from 1-9 and. 4 is the centre value. 
   *  Set the speed and the direction based on the value
   */
   
  if (y > 4) {
    directionY = "UP";
    directionYSpeed = map(y, 4, 9, 0, 4);
  } else if (y < 4)  {
    directionY = "DOWN";
    directionYSpeed = map(y, 4, 0, 0, 4);
  } else {
    directionY = "CENTRE";
    directionYSpeed = 0;
  }
  delay(20);
}
void printControllerValues() {
  Serial.println("MODE: " + String(mode) + " Direction: " + directionY + directionX + " XSpeed: " + directionXSpeed + " YSpeed: " + directionYSpeed);
}

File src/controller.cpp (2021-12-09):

#include <SPI.h>
#include <RF24.h>

/**
 *  Controller mode button pins
 */

#define button1 2
#define button2 3
#define button3 4
#define button4 5
#define button5 6

/**
 * Radio setup pins and address to send the data to
 */
const byte address[6] = "00001";
RF24 radio(9, 10);
bool radioReady = false;
int currentMode = 1;

/**
 * setup analogstick/joystick pins
 */
#define joyX A0
#define joyY A1

int xValue, yValue;

void setup() {
 
  // Initialise Serial first
  Serial.begin(9600);  // Baud rate
  // Pin modes
  // Configure the Radio
  setupButtons();
  setupRadio();
}

void setupButtons() {
  pinMode(button1, INPUT);
  pinMode(button2, INPUT);
  pinMode(button3, INPUT);
  pinMode(button4, INPUT);
  pinMode(button5, INPUT);
}

void setupRadio() {
  int failCount = 0;
  while (!radioReady && failCount < 10) {
    radioReady = radio.begin();
    if (!radioReady) {
      failCount++;
      Serial.print("Radio Initialisation Failed ");
      Serial.print(failCount);
      Serial.println(" times.");
    }
  }
  if (!radioReady) {
    Serial.println("Radio could not be initialised!");
    return;
  } else {
    Serial.println("Radio Ready!");
  }
  radio.setPALevel(RF24_PA_MIN); // Maximum Range
  radio.openWritingPipe(address); // For Outgoing Data
  radio.stopListening();
}

void loop() {

  if (digitalRead(button1)) {
    currentMode = 1;
    Serial.println("Button 1 PRESSED");
  } else if (digitalRead(button2)) {
    currentMode = 2;
    Serial.println("Button 2 PRESSED");
  } else if (digitalRead(button3)) {
    currentMode = 3;
    Serial.println("Button 3 PRESSED");
  } else if (digitalRead(button4)) {
    currentMode = 4;
    Serial.println("Button 4 PRESSED");
  } else if (digitalRead(button5)) {
    currentMode = 5;
    Serial.println("Button 5 PRESSED");
  }

/**
 * Read the value out from the joysticks and create a command for the buggy in the following format:
 * M=1X=1Y=1
 * 
 * M = 1-5
 * X = 1-9 (4 = center)
 * Y = 1-9 (4 = center)
 */

  xValue = analogRead(joyX);
  yValue = analogRead(joyY);

  int x1 = map(xValue, 0, 1023, 0, 9);  // 0 is our minimum speed and 9 is the maximam
  int y1 = map(yValue, 0, 1023, 0, 9);  

  String command = "M=" + String(currentMode) + "X=" + String(x1) + "Y=" + String(y1);
  Serial.println(command);
  int command_len = command.length() + 1;
  char command_array[command_len];
  command.toCharArray(command_array, command_len);
  radio.write(&command_array, command_len);
}

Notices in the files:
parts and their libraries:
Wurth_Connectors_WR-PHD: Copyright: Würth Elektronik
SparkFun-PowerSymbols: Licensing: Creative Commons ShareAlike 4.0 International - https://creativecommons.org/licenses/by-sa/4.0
